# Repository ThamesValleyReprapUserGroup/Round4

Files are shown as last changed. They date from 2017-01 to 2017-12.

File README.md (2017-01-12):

This is the repro for Round 4.

Currently round 4 is a Mendel90 frame with a build volume of 200x200x200mm

But we have put our own twist's on it:

- All wires are run on top side of the base plate
- The endstop is a minimum endstop and not a maximum one
- The X carriage is Prusa I3 style
- The sheets can be used by both new builders and the ones that has a Round1-3 printer
- Builder has option to use either a 12V 30A type PSU or an ATX PSU
- The sheet also have holes for an optional enclosure found on thingiverse here: http://www.thingiverse.com/thing:755654 and here http://www.thingiverse.com/thing:744868

The reasons for this are:

- Wires run on the underside tends to get caught to easy and flop arround. And we can loose the alu tubes which again have very hard to print/use endcaps.
- Max mounted endstops have its advantages but you have to home up with them and hence you have to go all the way down again before you can print. 
- Going for the Prusa I3 carriage gives more options as a lot more have been build for it
- We aim to be able to provide a set of sheets which can suit both upgrades and new builds
- Giving the choice of PSU let's the builder choose free. ATX's needs to be modded to work right (need to dummy loads added)
- An enclosure is almost a MUST HAVE if you want to print in ABS and have good results. This is optional thou but the holes for it will be on the sheets

 The BOM is here, it might need some tweaks so it can change as we get closer: https://docs.google.com/spreadsheets/d/1C7syP7WIMzRRcczZF0KAYDTLpP77kqbQEB_rWFmMJsc/edit?usp=sharing

 CURRENT STATUS: Verifying printed parts
 ---------------------------------------

We want to test that all the printed parts come out right on a calibrated printer.

This is done by printing and then messure all nut traps etc against this info sheet: 

http://www.slideshare.net/tejasudas/dimensions-of-metric-hex-nuts

First batch of "test" parts has been printed with Form Futura Easyfil ABS at 235C and 110C on the bed.

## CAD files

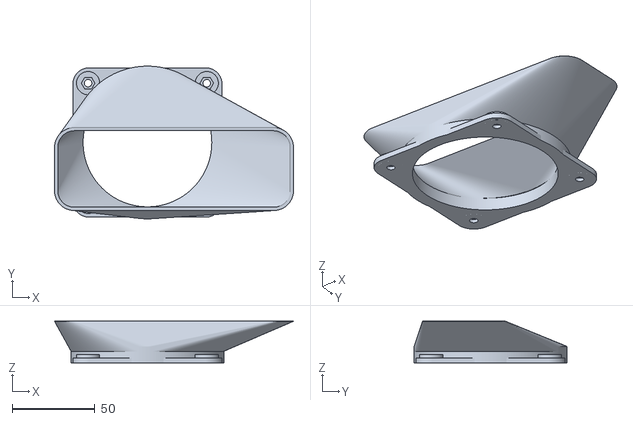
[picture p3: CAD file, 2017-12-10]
Mk42 Version/Printed Parts/Optinals/Bed fan duct/Mendel90_Fanduct_Heatbed.stl
144.0 x 92.0 x 25.1

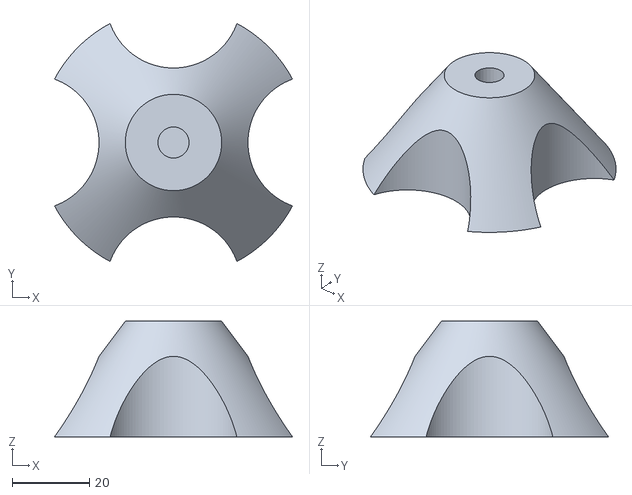
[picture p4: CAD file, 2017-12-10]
Mk42 Version/Printed Parts/Optinals/spool_holder.stl
61.8 x 61.8 x 30.0

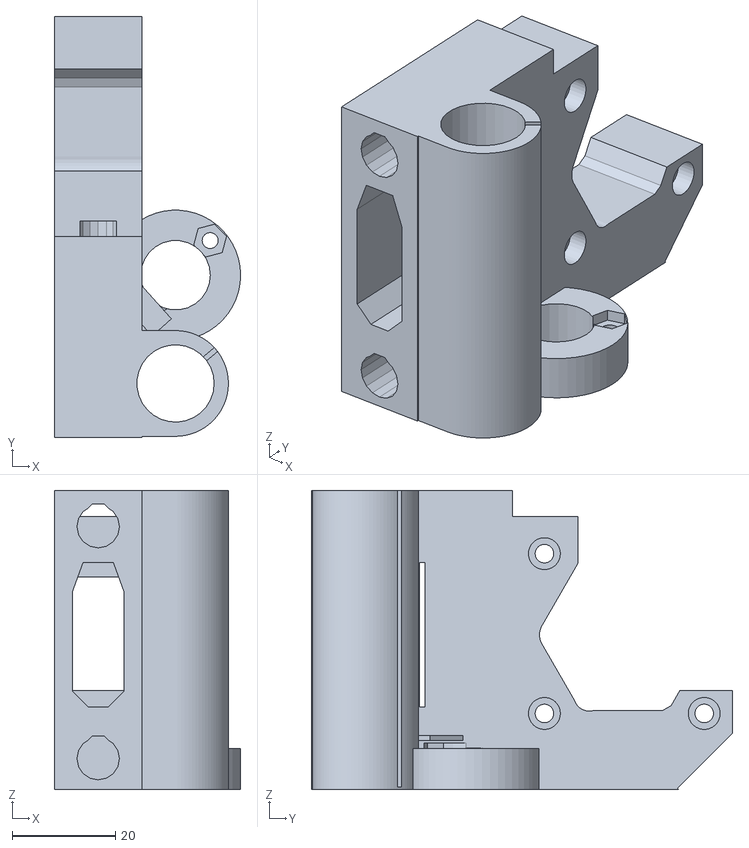
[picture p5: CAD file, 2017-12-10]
Mk42 Version/Printed Parts/X ends 2/x-end-motor.stl
36.1 x 81.7 x 58.0

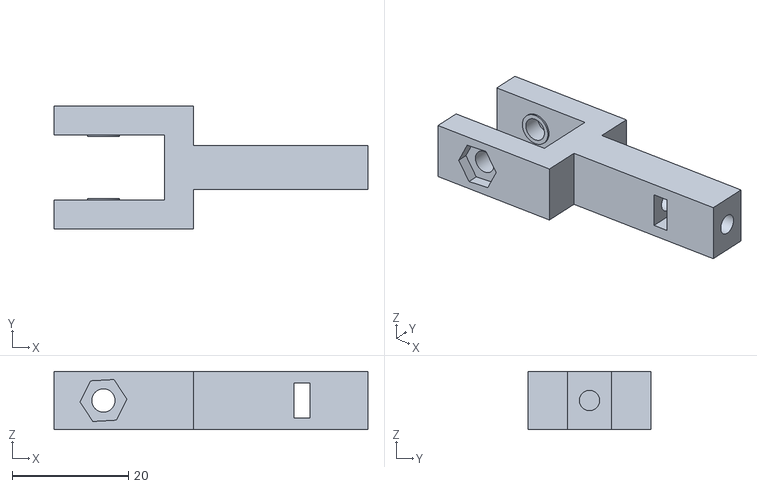
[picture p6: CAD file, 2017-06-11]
Mk42 Version/Printed Parts/Y Idler Fork.stl
54.0 x 21.2 x 10.0

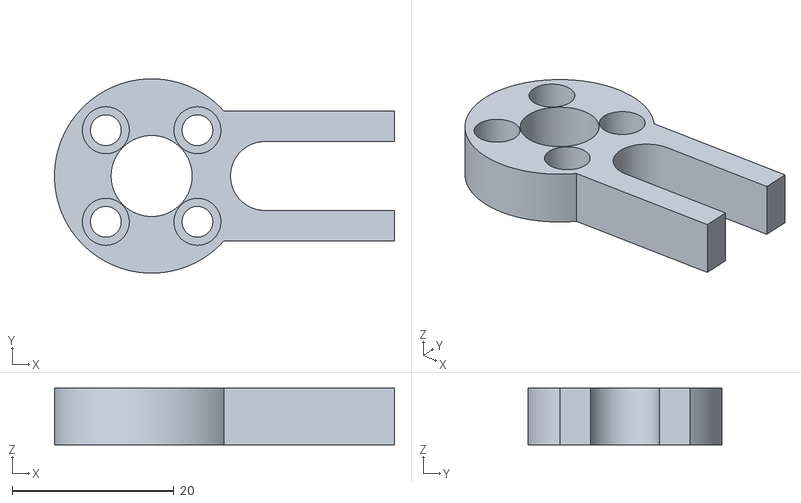
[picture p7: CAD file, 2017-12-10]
Mk42 Version/Printed Parts/Z isolators/dp-trapezoidal-zizolator.stl
42.0 x 24.0 x 7.00

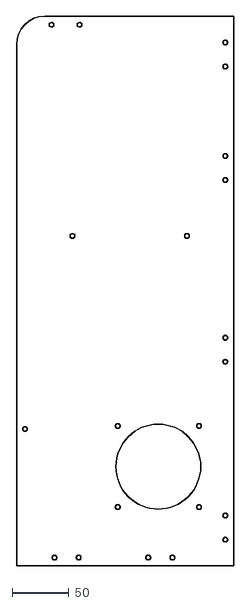
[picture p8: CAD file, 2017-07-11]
Mk42 Version/Sheets/frame_left_mk42_clean_fixed.dxf
191.1 x 484.0

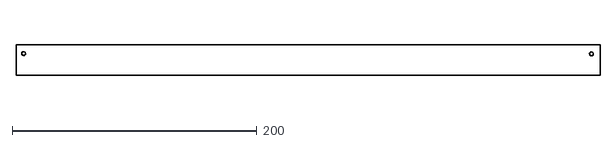
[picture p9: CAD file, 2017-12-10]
Mk42 Version/Sheets/Optional rear housing/coverplates_front_top_mk42_1.dxf
477.0 x 25.0

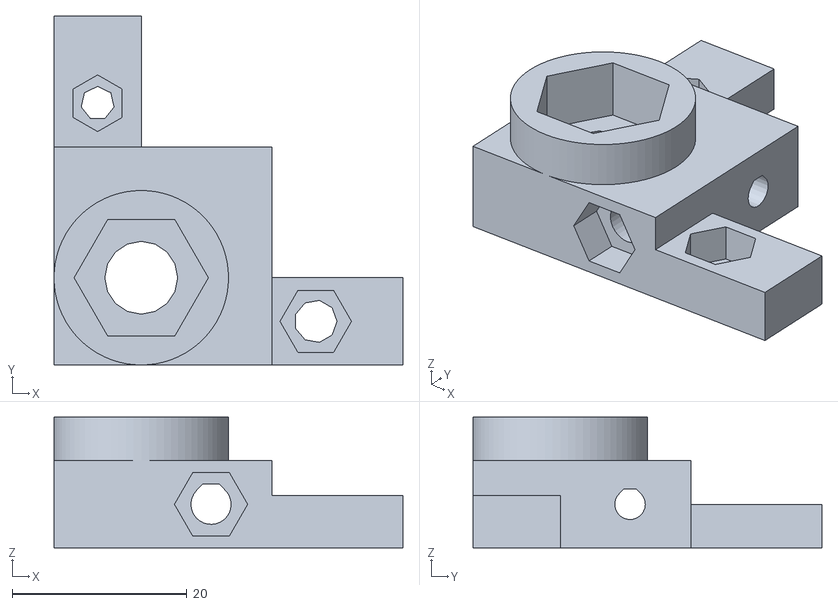
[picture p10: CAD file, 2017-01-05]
Calibration Prints/cal.stl
40.0 x 40.0 x 15.0

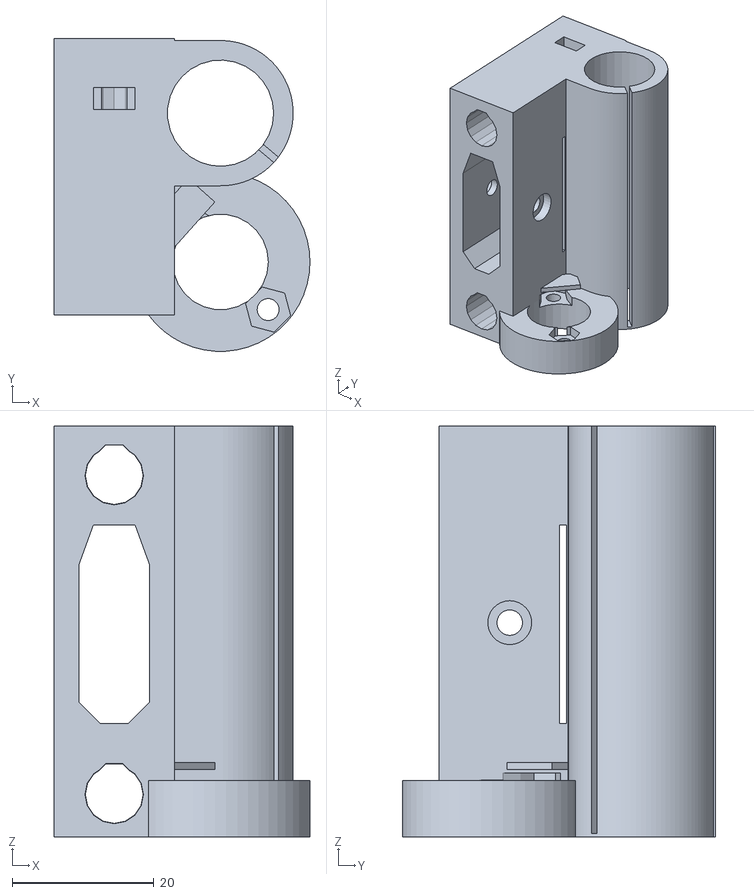
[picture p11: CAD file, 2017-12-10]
Mk42 Version/Printed Parts/X ends 2/x-end-idler.stl
36.1 x 44.1 x 58.0

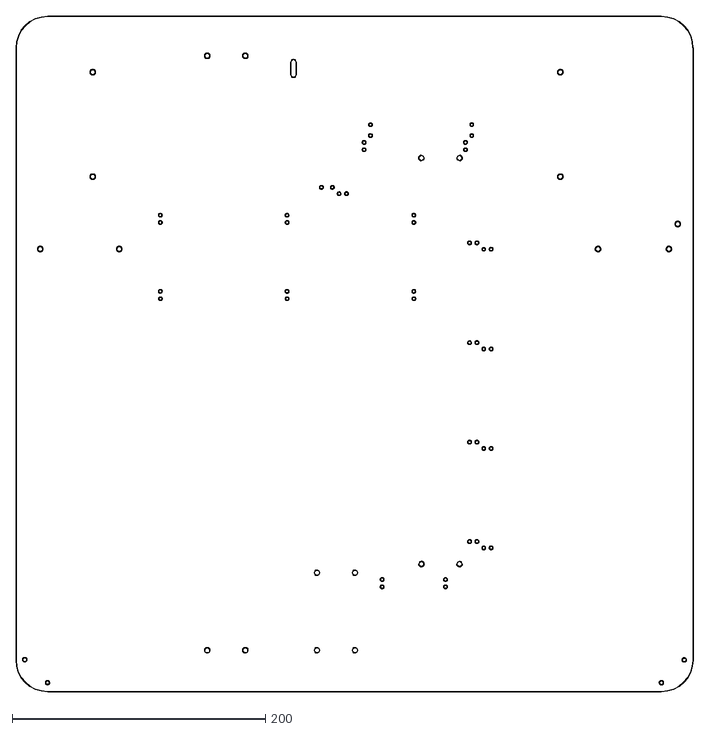
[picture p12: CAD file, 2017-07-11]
Mk42 Version/Sheets/frame_base_mk42_clean_fixed.dxf
534.2 x 532.7

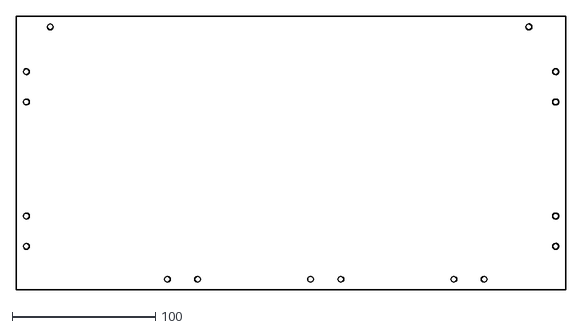
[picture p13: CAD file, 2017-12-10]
Mk42 Version/Sheets/Optional rear housing/coverplates_rear_2_mk42.dxf
383.8 x 190.7

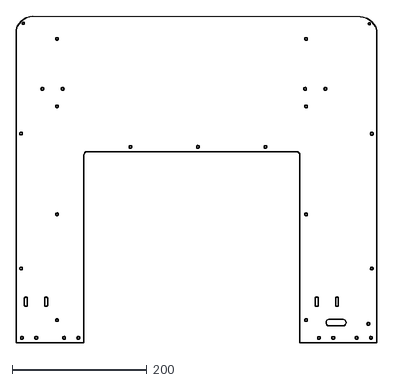
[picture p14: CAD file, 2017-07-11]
Mk42 Version/Sheets/frame_gantry_mk42_clean_fixed.dxf
534.4 x 483.9

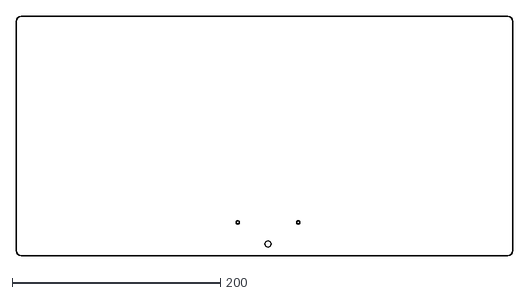
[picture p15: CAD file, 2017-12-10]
Mk42 Version/Sheets/Optional rear housing/coverplates_front_top_mk42_3.dxf
477.0 x 230.0

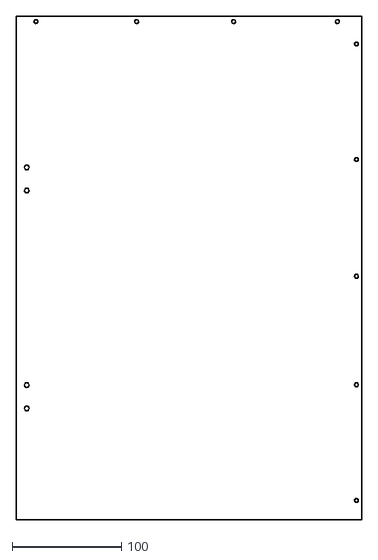
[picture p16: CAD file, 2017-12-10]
Mk42 Version/Sheets/Optional rear housing/coverplates_front_side_mk42.dxf
316.9 x 461.7

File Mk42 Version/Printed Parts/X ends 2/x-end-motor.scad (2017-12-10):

// PRUSA iteration3
// X end motor
// GNU GPL v3
// Josef Průša <iam@josefprusa.cz> and contributors
// http://www.reprap.org/wiki/Prusa_Mendel
// http://prusamendel.org

use <x-end.scad>
use <bearing.scad>
use <polyholes.scad>

module x_end_motor_base(){
 mirror([0,1,0])translate([0,18.2,0])x_end_base();
   
 translate(v=[-15,31,26.5]) cube(size = [17,44,53], center = true);
}

module x_end_motor_endstop_base(){
    translate([-23.5,-28.5,58]){
        difference(){
            // Base block
            cube([17,18.2,4]);
            // Nice edge
            translate([-1,10,10])rotate([-45,0,0])cube(20,20,20);
            } 
        }
}

module x_end_motor_endstop_holes(){
    translate([-23.5,-28.5,58]){
        translate([17/2,7.5,-3]){
            // Back screw hole for endstop
            translate([-4.75,0,0])cylinder(r=1,h=19,$fn=20);
            // Front screw hole for endstop
            translate([4.75,0,0])cylinder(r=1,h=19,$fn=20);
            }
        }
}

module x_end_motor_holes(){
 mirror([0,1,0])translate([0,18.2,0])x_end_holes();
 // Position to place
 translate(v=[-1,32,30.25]){
  // Belt hole
  translate(v=[-14,1,0]) cube(size = [10,46,22], center = true);
  // Motor mounting holes
  translate(v=[20,-15.5,-15.5]) rotate(a=[0,-90,0]) rotate(a=[0,0,90]) cylinder(h = 70, r=1.8, $fn=30);
  translate(v=[1,-15.5,-15.5]) rotate(a=[0,-90,0]) rotate(a=[0,0,90]) cylinder(h = 10, r=3.1, $fn=30);
  translate(v=[20,-15.5,15.5]) rotate(a=[0,-90,0]) rotate(a=[0,0,90]) cylinder(h = 70, r=1.8, $fn=30);
  translate(v=[1,-15.5,15.5]) rotate(a=[0,-90,0]) rotate(a=[0,0,90]) cylinder(h = 10, r=3.1, $fn=30);
   translate(v=[20,15.5,-15.5]) rotate(a=[0,-90,0]) rotate(a=[0,0,90]) cylinder(h = 70, r=1.8, $fn=30);
  translate(v=[1,15.5,-15.5]) rotate(a=[0,-90,0]) rotate(a=[0,0,90]) cylinder(h = 10, r=3.1, $fn=30);
  translate(v=[20,15.5,15.5]) rotate(a=[0,-90,0]) rotate(a=[0,0,90]) cylinder(h = 70, r=1.8, $fn=30);
  translate(v=[1,15.5,15.5]) rotate(a=[0,-90,0]) rotate(a=[0,0,90]) cylinder(h = 10, r=3.1, $fn=30);

  // Material saving cutout 
  translate(v=[-10,12,10]) cube(size = [60,42,42], center = true);

  // Material saving cutout
  translate(v=[-10,40,-30]) rotate(a=[45,0,0])  cube(size = [60,42,42], center = true);
  // Motor shaft cutout
  //#translate(v=[0,0,0]) rotate(a=[0,-90,0]) rotate(a=[0,0,90]) cylinder(h = 70, r=17, $fn=6);
 }
}

// Motor shaft cutout
module x_end_motor_shaft_cutout(){
    union(){
    difference(){
        translate(v=[0,32,30]) rotate(a=[0,-90,0]) rotate(a=[0,0,90]) cylinder(h = 70, r=17, $fn=6);
       
        translate(v=[-10,-17+32,30]) cube(size = [60,2,10], center = true);
        translate(v=[-10,-8+32,-15.5+30]) rotate(a=[60,0,0]) cube(size = [60,2,10], center = true); ///
        translate(v=[-10,8+32,-15.5+30]) rotate(a=[-60,0,0]) cube(size = [60,2,10], center = true);
        
        
    }
    translate(v=[-30,25.2,-11.8 +30]) rotate(a=[0,90,0]) cylinder(h = 30, r=3, $fn=30);
    translate(v=[-30,19.05,30]) rotate(a=[0,90,0]) cylinder(h = 30, r=3.5, $fn=100);
}
}




// Final part
module x_end_motor(){
 difference(){
     union(){
            x_end_motor_base();
            //x_end_motor_endstop_base();
         }
  x_end_motor_shaft_cutout();
  x_end_motor_holes();
  //x_end_motor_endstop_holes();    
      
      translate([-12,-42,65]) rotate([-35,0,0])  rotate([0,0,45]) cube(10,10,10);
      translate([-15,8.5,6]) rotate([90,0,0]) cylinder(h=5, r=5, $fn=30);   
      translate([-15,8.5,51]) rotate([90,0,0]) cylinder(h=5, r=5, $fn=30);   
      translate([-15,3.5,6]) rotate([90,0,0]) cylinder(h=3, r1=5, r2=4, $fn=30);   
      translate([-15,3.5,51]) rotate([90,0,0]) cylinder(h=3, r1=5, r2=4, $fn=30); 
      //#translate([-16,-40,0])cube([50,100,100]); 
        bearing_diameter = 14.5;
         thinwall = 3;
bearing_size = bearing_diameter + 2 * thinwall;
        
         
        translate(v=[0,-18.2,10]) poly_cylinder(h = 62, r=(bearing_diameter/2)+0.1);
         
 }
 
}

translate([0,-2.8,0])x_end_motor();

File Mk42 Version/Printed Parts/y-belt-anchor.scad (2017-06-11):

//
// Mendel90
//
// GNU GPL v2
// nop.head@gmail.com
// hydraraptor.blogspot.com
//
// Anchors the belt to the bottom of the y carriage
//
include <conf/config.scad>
include <positions.scad>

wall = 2;

clearance = 2;
thickness = M3_nut_trap_depth + bearing_clamp_tab_height;
rad = 3;

clamp_thickness = 2.8;

width = belt_width(Y_belt) + 3 + washer_diameter(M3_washer) + clearance;
inner_width = (M3_nut_radius + wall) * 2 ;
depth =  washer_diameter(M3_washer) + clearance;
length = depth + 2 * (2 * M3_nut_radius * cos(30) + wall);

tooth_height = belt_thickness(Y_belt) / 2;
tooth_pitch = belt_pitch(Y_belt);
tooth_width = tooth_pitch / 2;

function y_belt_anchor_width() = width;
function y_belt_anchor_depth() = depth;

module y_belt_anchor_holes() {
    for(side = [-1, 1])
        translate([0, side * (depth / 2 + M3_nut_radius * cos(30) + eta) + depth / 2, 0])
            children();

}

module y_belt_anchor(height, toothed) {
    h = height + belt_thickness(Y_belt) - belt_clearance;
    recess = length - depth;

    stl(str("y_belt_anchor", toothed ? "_toothed" : ""));
    union() {
        difference() {
            union() {
                translate([0, depth / 2, h / 2])                                                        // tall bit
                    rounded_rectangle([width, depth, h], r = rad);

                translate([0, depth / 2, thickness / 2])
                    rounded_rectangle([inner_width, length, thickness], r = rad);                       // wide bit

                for(side = [-1, 1])                                                                     // webs
                    for(end = [-1, 1])
                        translate([side * (M3_nut_radius + wall / 2 + eta), eta + (end + 1) * (depth / 2 - 2 * eta), thickness - eta])
                            rotate([90,0,90 * end])
                                right_triangle(width = (length - depth) / 2 - rad, height = h - thickness, h = wall);
            }


            translate([0, depth / 2, height + (h - height) / 2 + 2 * eta])                              // slot for belt
                cube([belt_width(Y_belt) + belt_clearance, depth + 1, h - height], center = true);

            for(side = [-1, 1]) {                                                                        // clamp screw nut traps
               # translate([side * (belt_width(Y_belt) / 2 + M3_clearance_radius), depth / 2, 0 ])
                    rotate([0,0,90/7 * (side + 1)])
                        nut_trap(M3_clearance_radius, M3_nut_radius+0.1, height - clamp_thickness);

                translate([0, side * (depth / 2 + M3_nut_radius * cos(30) + eta) + depth / 2, thickness])  // mounting screw nut traps
                    nut_trap(M3_clearance_radius, M3_nut_radius, M3_nut_trap_depth);

            }
            translate([0, depth / 2, height + (h - height) / 2 + 2 * eta])                                  // slot to join screw holes
                cube([belt_width(Y_belt) + M3_clearance_radius * 2, corrected_diameter(M3_clearance_radius * 2), h - height], center = true);
        }

        for(side = [-1, 1])                                                                                 // blind the nut traps
            translate([side * (belt_width(Y_belt) / 2 + M3_clearance_radius), depth / 2, height - clamp_thickness])
                cylinder(r =  M3_clearance_radius + 0.5, h = layer_height + eta);

        if(toothed)
            for(i = [-1:1])
                if(abs(i) * tooth_pitch + tooth_width / 2 < depth / 2)
                    translate([0, depth / 2 + i * tooth_pitch, height - eta + tooth_height / 2])
                        cube([belt_width(Y_belt), tooth_width, tooth_height], center = true);
    }
}

module y_belt_clip(toothed) {
    stl(str("y_belt_clip",  toothed ? "_toothed" : ""));

    union() {
        translate([0, 0, clamp_thickness / 2]) difference() {
            rounded_rectangle([width, depth, clamp_thickness], r = rad);

            for(side = [-1, 1])                                                                        // screw holes
                translate([side * (belt_width(Y_belt) / 2 + M3_clearance_radius), 0, 0 ])
                    poly_cylinder(r = M3_clearance_radius, h = clamp_thickness + 1, center = true);
        }
        if(toothed)
            for(i = [-1:1])
                if(abs(i) * tooth_pitch + tooth_width / 2 < depth / 2)
                    translate([0, i * tooth_pitch, clamp_thickness - eta + tooth_height / 2])
                        cube([belt_width(Y_belt), tooth_width, tooth_height], center = true);
    }

}

module y_belt_anchor_assembly(height, toothed) {
    //assembly("y_belt_anchor_assembly");

    color(y_belt_anchor_color) render() y_belt_anchor(height, toothed);

    translate([0, depth / 2, height + belt_thickness(Y_belt) + clamp_thickness]) {
        rotate([180, 0, 0])
            color(y_belt_clip_color) render() y_belt_clip(!toothed);
        //
        // Clamp screws
        //
        for(side = [-1, 1])
            translate([side * (belt_width(Y_belt) / 2 + M3_clearance_radius), 0, 0]) {
                screw_and_washer(M3_cap_screw, 16);
                translate([0, 0, -2 * clamp_thickness - belt_thickness(Y_belt)])
                    rotate([180, 0, 90/7 * (side + 1)])
                        nut(M3_nut, true);
            }
    }
    for(side = [-1, 1])
        translate([0, side * (depth / 2 + M3_nut_radius * cos(30) + eta) + depth / 2, 0]) {
            translate([0, 0, thickness - M3_nut_trap_depth])
                nut(M3_nut, true);
            translate([0, 0, - sheet_thickness(Y_carriage)])
                rotate([180, 0, 0])
                    screw_and_washer(M3_cap_screw, 16);
        }

    //end("y_belt_anchor_assembly");
}

module y_belt_anchor_stl()         y_belt_anchor(Y_belt_clamp_height, false);
module y_belt_anchor_toothed_stl() y_belt_anchor(Y_belt_clamp_height, true);
module y_belt_clip_stl()           y_belt_clip(false);
module y_belt_clip_toothed_stl()   y_belt_clip(true);

module y_belt_anchors_stl() {
    translate([0,  0, 0]) y_belt_anchor_toothed_stl();
    translate([0, 25, 0]) y_belt_anchor_stl();
//    translate([15, 5, 0]) rotate([0,0,90])y_belt_clip_toothed_stl();
//    translate([15,30, 0]) rotate([0,0,90]) y_belt_clip_stl();
}

//if(1)
  //  y_belt_anchor_assembly(Y_belt_clamp_height, true);
//else
    y_belt_anchors_stl();

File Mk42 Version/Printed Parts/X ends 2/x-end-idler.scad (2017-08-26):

// PRUSA iteration3
// X end idler
// GNU GPL v3
// Josef Průša <iam@josefprusa.cz> and contributors
// http://www.reprap.org/wiki/Prusa_Mendel
// http://prusamendel.org

use <x-end.scad>



module x_end_idler_holes(){
    x_end_holes();
    translate([0,3.5,0]){
    translate(v=[0,-22,30.25]) rotate(a=[0,-90,0]) cylinder(h = 80, r=1.8, $fn=30);
    translate(v=[1.5,-22,30.25]) rotate(a=[0,-90,0]) cylinder(h = 10, r=3.1, $fn=30);
    translate(v=[-21.5,-22,30.25]) rotate(a=[0,-90,0]) rotate(a=[0,0,30]) cylinder(h = 80, r=3.2, $fn=6);
        
 }
}


module waste_pocket(){
 // waste pocket
    translate([-15,-1,6]) rotate([90,0,0]) cylinder( h=5, r=5.5, $fn=30);     
    translate([-15,-1,51]) rotate([90,0,0]) cylinder( h=5, r=5.5, $fn=30);    
    translate([-15,-5.9,6]) rotate([90,0,0]) cylinder( h=3, r1=5.5, r2=4.3, $fn=30);     
    translate([-15,-5.9,51]) rotate([90,0,0]) cylinder( h=3, r=5.5, r2=4.3, $fn=30);      

    
    //M3 thread
    translate([-15,8.5,6]) rotate([90,0,0]) cylinder( h=12, r=1.4, $fn=30); 
    translate([-15,8.5,51]) rotate([90,0,0]) cylinder( h=12, r=1.4, $fn=30); 

    //M3 heads
    translate([-15,11.5,6]) rotate([90,0,0]) cylinder( h=4, r=2.9, $fn=30); 
    translate([-15,11.5,51]) rotate([90,0,0]) cylinder( h=4, r=2.9, $fn=30); 

    //M3 nut traps
    translate([-17.9,0.5,52-3-1.6]) cube([5.8,3.1,20]);
    translate([-17.9,0.5,-10+1.5+1.6]) cube([5.8,3.1,16]);
}


module x_end_idler_base(){
    union(){
        difference(){
            x_end_base();
            x_end_idler_holes();
        }
        translate([-15,8.5,6]) rotate([90,0,0]) cylinder( h=11, r=6, $fn=30);
        translate([-15,8.5,51]) rotate([90,0,0]) cylinder( h=11, r=6, $fn=30);
    }
}


module x_end_idler(){
    //mirror([0,1,0]) 
    difference(){
        x_end_idler_base();
        waste_pocket();
        
  // Bottom pushfit rod
translate(v=[-15,-31.2,6]) rotate(a=[-90,0,0]) pushfit_rod(7.8,41);
// Top pushfit rod
translate(v=[-15,-31.2,45+6]) rotate(a=[-90,0,0]) pushfit_rod(7.8,41);
    }
    
}
//difference(){
x_end_idler();
//translate([-15,-50,0])   cube([100,100,100]);
//}

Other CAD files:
Mk42 Version/Sheets/y_heatshield.dxf
Mk42 Version/Sheets/Optional rear housing/coverplates_rear_1_mk42.dxf
Mk42 Version/Sheets/y_heatshield_2.dxf
Mk42 Version/Printed Parts/X ends 2/x-end.scad
Calibration Prints/20140205_Marvin_KeyChain.STL
Mk2 version/Printed Parts/3edv6mount/Bowden_carriage.stl
Mk2 version/Printed Parts/3edv6mount/Bowden_carriage_clamp.stl
Mk2 version/Printed Parts/Optionals/Bed fan duct/Mendel90_Fanduct_Heatbed.scad
Mk2 version/Printed Parts/Optionals/Bed fan duct/Mendel90_Fanduct_Heatbed.stl
Mk2 version/Printed Parts/Optionals/Filament_holder.scad
Mk2 version/Printed Parts/Optionals/Filament_holder.stl
Mk2 version/Printed Parts/Optionals/Ramps Holder with 80mm fan option/arduino_carrier2p_base.stl
Mk2 version/Printed Parts/Optionals/Ramps Holder with 80mm fan option/carrier2p_frame.stl
Mk2 version/Printed Parts/Optionals/duet enclosure/Duet_enclosure.stl
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

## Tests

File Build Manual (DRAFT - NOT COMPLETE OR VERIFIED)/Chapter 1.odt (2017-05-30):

## 1. General Build Tips

- X is left / right. Y is backwards / forwards. Z is up / down.
- De-grease the rods. Acetone or methylated spirit works. Dont worry they will be oiled later.
- All screws have a plain washer where they meet the plastic/sheets, to spread the load and prevent the plastic being chewed up by the rotation of the screw head. Most fixings have a captive Nyloc nut to prevent them vibrating loose. It is very important that the nut is fully seated in the nut trap while the screw is inserted. They are quite a tight fit, so sometimes it is necessary to pull or push them in with a long screw.
- The X and Y bar clamps should not be over tightened, i.e. do not close the gap fully or the parts will break. The Y and Z bars only need a light clamping force because the only force trying to slide them is the bearing friction.
- Washers tend to have a smooth side and a side with a burr from being stamped out. Make sure the smooth side faces bearings and belts.

NOTE: During this manual 3mm fiberboard was used. It’s cheaper for prototyping.

NOTE: It’s optional, but might be a good idea to drill all holes to their spec’ed size. If a 4mm screw is used in the hole drill it to 4mm. Endstop switches normally 2.5 holes but you can drill them to 3mm if you talke care. This is the method used in this manual.

### Tools Required

- Allen keys: 1.5 & 2.5mm & 3mm
- Needle nose pliers.
- 8mm sharp drill bit
- 3mm
- 4mm
- 2mm
- Drill with variable speed
- Small hammer
- Marker or pen
- M3 tap
- Wire cutters.
- Wire strippers.
- Crimp tool for dupont connectors – You can solder but its not nearly as good as crimping

#### Recommended

- Multi-meter
- Digital callipers.
- Dial gauge and/or Set of feeler blades(to level the bed more - precise than paper method)
- Heat gun for heat shrink tubing… far better than lighter or soldering iron
- Ruler and square. Even thou it should be 90 degrees, it does not hurt to check.

#### Consumables

- oil, white lithium grease, alcohol (for cleaning bed), lint free wipes.

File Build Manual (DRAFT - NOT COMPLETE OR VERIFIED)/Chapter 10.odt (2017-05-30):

## 10. Y Carriage Assembly

### Vitamins

14 M3 cap screw x 16mm 1 Dibond sheet 216mm x 216mm x 3mm 3 LM8UU bearings | 14 Nyloc nut M3 14 Washer M3 x 7mm x 0.5mm 3 Zip-tie 100mm min length

### Printed parts


| | 3 y_bearing_mount.stl

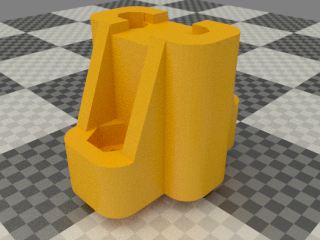
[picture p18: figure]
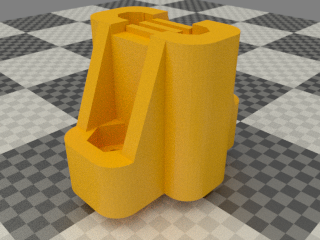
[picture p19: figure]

1 y_belt_anchor.stl | 1 y_belt_anchor_toothed.stl

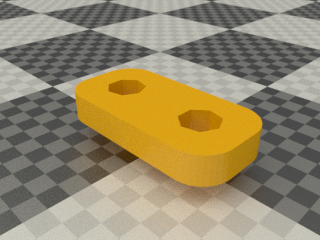
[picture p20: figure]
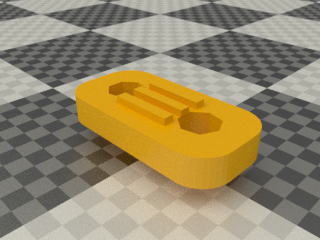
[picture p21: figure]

1 y_belt_clip.stl | 1 y_belt_clip_toothed.stl

### Assembly

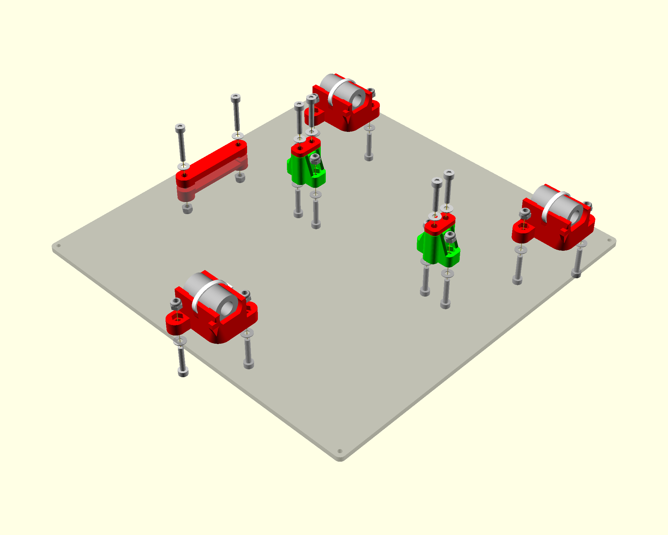
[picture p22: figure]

This view is from the bottom of the bed which is the matt side of the Dibond. The nuts go on the bottom and the screw heads and washers on top.

1. Insert M3 nyloc nuts into all of the nut traps, including those that go all the way up to the top of the belt anchors. A long M3 screw can be used to pull them up to the top.
2. Tie the bushingss into the holders with the zip ties, and screw the holders to the carriage using M3 x 16mm screws and washers. Note that one side of the bearing holders has a tab to trigger the limit switch and that must face forwards (that is, away from the ribbon clamp).
  TIP: use the square to help make the rod and holders parallel to the edge
3. Align the two bearings on the left (right on the picture) by inserting a rod and lining up the tabs with the edge of the board before tightening the screws. Leave the third bearing loose.
4. Fit the belt clamps loosely to retain the nuts using M3 x 16mm screws and washers, then fit the anchors to the carriage using M3 x 16mm screw and washers. Note that the anchor with the teeth goes at the back (nearest to the ribbon clamp) and the belt clamp with the teeth at the front.

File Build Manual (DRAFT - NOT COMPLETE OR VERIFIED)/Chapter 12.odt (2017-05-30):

## Print bed assembly

### Vitamins

1 PCB bed mk42 4 M3 cap screw x 10mm 6 Hex male / female pillar M3 x 20mm | 2 Heatshrink sleeving ID 1.6mm x 15mm 2 Heatshrink sleeving ID 2.4mm x 15mm 2 Heatshrink sleeving ID 6.4mm x 30mm 4 Washer M3 x 7mm x 0.5mm 1 Black wire 32/0.2 length 635mm 1 Red wire 32/0.2 length 620mm

### Sub-assemblies

1 y_carriage_assembly

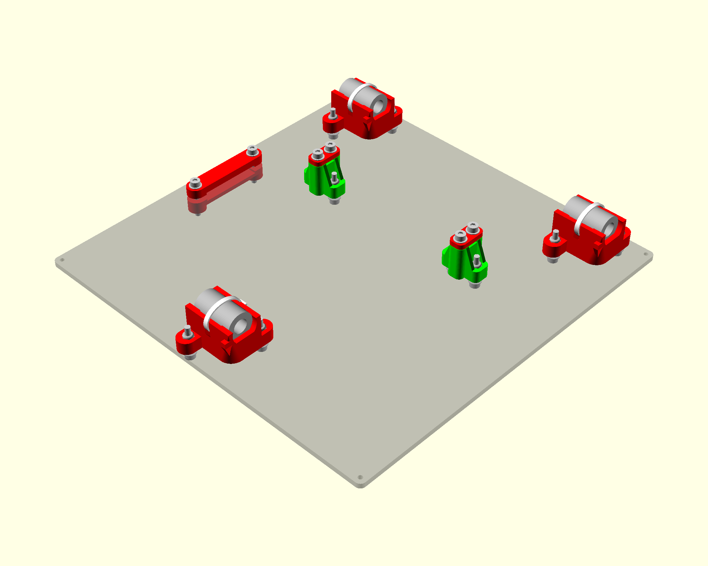
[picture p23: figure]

### Bed Wiring

1. Solder the red wire to the positive terminal and the black to negative.
2. Place a strip of kapton tape where the thermistor wires will go.
3. Use kapton tape to tape down the thermistor. Place the thermistor at the center hole. Don’t force it in but just let it rest there.
4. Use red and black wires trimmed from the X motor for the thermistor wiring extension.
5. Insert the hex screws at each corner and the 2 near the center
6. mount the heat bed with 6 countersink screws
7. attach the wires to the zip ties to the holes going from the corner towards the center.
8. Fold the wires over the edge near the center and attach to carraige with the holes going from the edge at the center towards the center

### Assembly

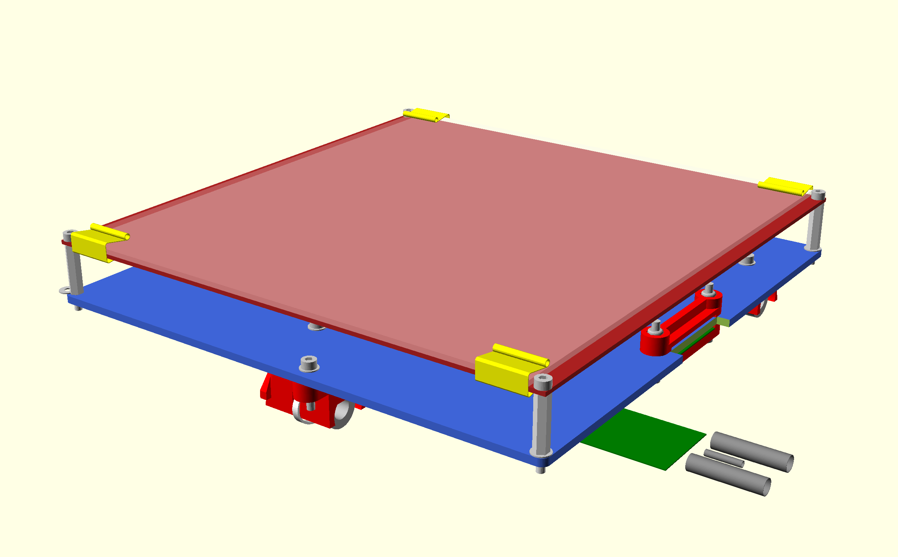
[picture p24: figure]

1. Tap the corner holes and the 2 center holes to 3mm. Screw the pillars into the Y carriage, but don't over tighten as it is quite soft. Note that the rear two pillars have a washer under them. The front two are initially spaced the same distance by using a washer as a temporary shim. They can then be adjusted up or down slightly to level the bed relative to the nozzle.
2. The bed is installed with the cable at the back. It initially leads off forwards and then loops back on itself under the top ribbon clamp. It then doubles back under the Y carriage through the lower cable clip.
3. Screw the bed to the top of the pillars with the M3 x 10 cap screws (no washers). Just start the screws as you will need to take the bed off again to tighten the last bearing holder. This is best done when belt etc. are in place

TO BE DONE: DP notes says to use button head screws as they reduce height and interference with HE and then no PP strip used?

4. Pull the ribbon cable tight enough so that the loop under the bed does not touch the bed and clamp it together with the polypropylene strip (which goes closest to the clamp).

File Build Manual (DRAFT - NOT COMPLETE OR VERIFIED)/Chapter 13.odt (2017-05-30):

## Y Axis Assembly

### Vitamins

1 Belt GT2 x 6mm x 662mm 4 M3 cap screw x 16mm 8 M4 cap screw x 16mm 4 Nyloc nut M3 8 Nyloc nut M4 2 No2 pan wood screw x 13mm | 1 Smooth rod 8mm x 270mm 1 Smooth rod 8mm x 417mm 1 Microswitch 2 Washer M2.5 x 5.9mm x 0.5mm 4 Washer M3 x 7mm x 0.5mm 8 Washer M4 x 9mm x 0.8mm

### Printed parts

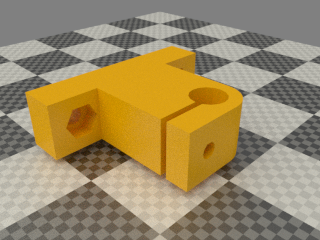
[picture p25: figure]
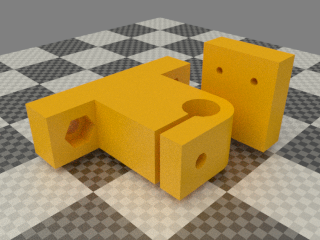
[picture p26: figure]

3 y_bar_clamp.stl | 1 y_bar_clamp_switch.stl

### Sub-assemblies

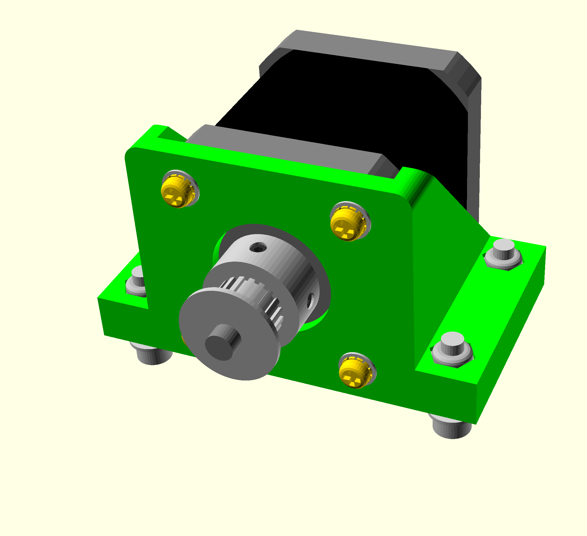
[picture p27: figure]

1 print_bed_assembly | 1 y_idler_assembly | 1 y_motor_assembly

### Assembly


1. Drill the 2 small holes in the switch bar clamp to 2.5mm
2. tap the holes to 3mm
3. Insert the captive nyloc M3 nuts and M3 x 16mm cap screws in each of the Y bar clamps.
4. Loosely fit the two left hand Y bar clamps to the base. Orientate them so the rod is towards the outside of the machine.
5. Twist together two green wires about 750mm long (trimmed from the X motor) and solder them to the outer two pins of the microswitch. Reem out the holes in the microswitch and attach it to the barclamp with M3 screws with M3 screws BUT NO wshers as it would prevent the smooth rod from going in the bar clamp. Remember the button towards the top and facing the back of the machine.
6. Fit the right hand Y bar clamps to the base but leave the screws loose.
7. Thread the limit switch wires through the zip ties and through mouse hole in the right stay.
8. Also thread the Y motor wires through the zip ties in the base and then screw the Y motor bracket in place. Run the wires in the cable ties and holes parallel to the limit switch wires.
9. Clamp the Y belt in the front belt anchor with the teeth facing away from the carriage. The end of the belt should project enough to have five complete teeth showing.
10. Put a half twist in the belt and then thread it through the Y idler assembly with the smooth side against the bearings and then clamp it in the rear clamp with the teeth facing the carriage. Again leave five complete teeth projecting from the anchor.
11. Slide the Y bars through the bar clamps and the carriage bearings. Tighten the clamps to grip the bars lightly but do not over-tighten them. Slide the carriage up and down to align the right hand bearing and bar clamps. Tighten the bearing first and then move it to each end and tighten the clamps.
12. Put the belt over the motor pulley and fasten the idler assembly to the base with enough tension on the belt to play a low note when plucked. Ensure the belt runs in the middle of the idler without touching the washers each side by adjusting the angle of the idler.
13. Attach the wires from the bed so that it forms a loop. The middle of the loops points towards the Y motor.
14. The wires turn right and go through the cable ties and under the mouse holes in the right hand stay. The heater wires go through the rear tie and the larger hole.

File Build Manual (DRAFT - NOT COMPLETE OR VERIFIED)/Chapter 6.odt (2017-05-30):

## 6 Motor Assemblies

### Vitamins

2 M3 cap screw x 16mm 4 M3 cap screw x 12mm 4 M4 cap screw x 16mm 2 NEMA17 x 47mm stepper motor 6 Nyloc nut M3 | 4 Nyloc nut M4 8 M3 cap screw x 10mm 14 Washer M3 x 7mm x 0.5mm 4 Washer M4 x 9mm x 0.8mm 8 Star washer M3 x 0.5mm

### Printed parts


1 z_motor_bracket_lhs.stl | 1 z_motor_bracket_rhs.stl


2 z-axis_lead_screw_clamp.stl

### Assembly

1. Fit all the nyloc nuts into their nut traps.
2. Fit the M3 x 16mm cap screws to the bar clamps with plain washers.
3. Attach the motor using four M3 x 10mm cap screws, star washers and plain washers. Wires from the left hand motor routes on top of the base to the left and meets up with the wires from the Y motor and goes through the gantry and under the right stay. The wires from the right hand motor goes through the wide slot just behind it.
4. Degrease the motor shafts before fitting the Z coupling, but be very carefull you dont get degreaser down the shaft in the steppers. Holding them upside down should help
5. Fit the coupling loosely for now. Insert a M3 screw and washer but do not tighten fully
6. Twist the motor wires in pairs. Red / blue are one pair and green / black the other pair. The quickest way to twist them is by using an electric drill. Tie a knot in the far end and put it in the chuck. The reason they are twisted is to minimise the radio frequency emissions.
7. Attach the motor assemblies to the gantry using M4 x 16mm cap screws and washers. Note that the motors rest on the base and the bar clamps face inwards.


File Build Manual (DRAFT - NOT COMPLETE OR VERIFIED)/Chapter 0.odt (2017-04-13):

# Mendel90 Instructions

The build is broken down into sub assemblies that can be worked on sequentially by one person, or in parallel if there is more than one person building. For this reason each assembly begins on a new page so the instructions can be separated.

15-11-12 First release of this manual.

25-11-12 Made Z cable 100mm longer. Added advice about temperatures.

03-12-12 Fixed missing Z parts. Added Skienforge and bed sections.

30-11-12 Z bar clamps and Y bearing mounts no longer have separate switch versions.

21-12-12 T2.5 belt and pulleys, new extruder PCB and Jhead mount.

02-01-13 Minor corrections and suggestions from users.

03-03-13 Removed feed tube connector.

14-03-13 Updates from user feed back and latest part renders.

21-03-13 Added section on using other software.

20-05-13 Added warning about absolute extrusion.

12-09-13 New X ends, Z couplers and fan bracket.

18-09-13 New file locations, SF profile, etc.

01-10-13 Updated remaining assembly views for black screws and red silicone on hot end.

18-11-13 Added instruction to fit nut and grub screw to extruder gear.

12-01-14 Fixed erroneous reference to hex screws in X motor assembly.

17-01-14 Added requirement for Philips screwdriver for removing X and E motor screws.

Fixed erroneous z_min instead of z_max.

17-01-14 Clarified changing E_STEPS_PER_MM expression.

27-07-14 Small corrections and clarifications.

07-09-14 Fixed a few typos.

14-10-14 Fixed more typos.

12-03-15 Added bed cooling fan wiring details.

08-06-15 Changed belts and pulleys to GT2

02-08-16 Changed by tvrrug.co.uk to have all wires run on top of the base. This makes the wire runs as short as possible and makes the chances of wires getting caught less.

02-08-16 Changed by tvrrug.co.uk to use the Prusa I3 X carriage system but with the X motor still on the right.

02-08-16 Changed by tvrrug.co.uk to use the Mk42 Bed.

02-08-16 Changed by tvrrug.co.uk to not use cable clamps. They are replaced with silicone/rubber wires held in place with zipties at each end

Table of Contents

1.General Build Tips 6

Tools Required 8

Recommended 8

Consumables 8

2.Frame Assembly 9

Vitamins 9

Printed parts 9

Assembly 10

3.Bed Fan Assembly 13

Vitamins 13

Printed part 13

Assembly 13

4.X Idler Assembly 15

Vitamins 15

Printed 15

Assembly 16

5.X Motor Assembly 17

Vitamins 17

Printed parts 17

Assembly 18

6.Z Motor Assemblies 23

Vitamins 23

Printed parts 23

Assembly 24

7.Z Axis Assembly 26

Vitamins 26

Printed parts 26

Sub-assemblies 26

Assembly 27

8.Y idler assembly 29

Vitamins 29

Printed parts 29

Assembly 29

9.Y motor assembly 30

Vitamins 30

Printed parts 30

Assembly 31

10.Y Carriage Assembly 32

Vitamins 32

Printed parts 32

Assembly 33

11.Y Heatshield Assembly 34

Vitamins 34

Assembly 34

12.Print bed assembly 35

Vitamins 35

Sub-assemblies 35

Bed Wiring 36

Assembly 38

13.Y Axis Assembly 39

Vitamins 39

Printed parts 39

Sub-assemblies 39

Assembly 40

14.X Carriage Fan Assembly 42

Vitamins 42

Printed parts 42

Assembly 42

15.X Carriage Assembly 43

Vitamins 43

Printed parts 43

Assembly 44

16.Hot end assembly 45

Vitamins 45

Assembly 45

17.Extruder connection PCB assembly 47

Vitamins 47

Assembly 47

18.Extruder Motor Assembly 48

Vitamins 48

Printed parts 48

Sub-assemblies 48

Assembly 49

19.Extruder Assembly 51

Vitamins 51

Printed parts 51

Sub-assemblies 51

Assembly 52

20.X Axis Assembly 55

Vitamins 55

Sub-assemblies 55

Assembly 56

21.Spool holder assembly 58

Vitamins 58

Printed parts 58

Assembly 59

22.PSU assembly 60

Vitamins 60

Printed parts 60

Wiring 61

Summary 62

Assembly 63

23.Electronics Assembly 64

Vitamins 64

Printed Parts 64

Assembly 64

24.Software 68

Marlin Firmware 68

Arduino IDE 68

Pronterface 68

25.Testing 70

Jumpers 70

Power up 70

Limit switches 70

Motors 70

Heaters 71

Fan 71

26.Calibration 72

Bed Levelling 72

Extruder Calibration 73

Z Home Point 73

First Print 74

Slicing with Skeinforge 75

Extrusion Limits 76

27.Operating Instructions 77

Heated Bed 77

Changing filament 77

Removal 77

Insertion 78

Different types of filament 78

Cleaning the hobbed bolt 79

Using Other Software Tools 80

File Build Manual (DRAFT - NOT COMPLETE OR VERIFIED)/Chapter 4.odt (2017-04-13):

## 4 X Idler Assembly

### Vitamins

2 Ball bearing 624 4mm x 13mm x 5mm 2 LM8UU bearings 1 M3 cap screw x 35mm 1 M4 cap screw x 25mm 1 M3 cap screw x 18mm 1 Nyloc nut M3 | 1 Nyloc nut M4 2 Washer M3 x 7mm x 0.5mm 2 Washer M4 x 9mm x 0.8mm 1 Nut M3 1 M5 Brass nut

### Printed


1 i3xends_v2_Idler.stl | 1 i3xends_v2_Idler_fork.stl | 1 z_screw_isolator_left.stl

REPLACE 624 normal bearings with flanged type. Fork can rotate and belt will rub on the plastic. Also there is only so much room

LONGER M3 screw needed for for the idler fork

### Assembly

1. Slide the 2 Idler parts together, they are a VERY tight fit. Don’t worry if they don’t slide completely together. When inserting the X rods they will home the last bit.
2. Insert a M3 Nut in the idler fork. Slide it in the idler bits and insert a M3 35mm cap screw with a washers from the end of the idler, make sure the screw engange the nut corretcly.
3. Insert the M4 screw and washer through the fork while adding in the following order: 2 624 bearings. Once the screw is through add the final M4 washer and then M4 nyloc.

TIP: wipe the bearings off with paper tissue before mounting them. There might be grease on them. DONT use alcohol etc. just paper tissue and elbow grease-

TIP: if the bearings are loose on the screw add equal amount of M4 washers on the outside of each bearing until the assembly fits snug

4. Insert 2 LM8UU bearings, one from the top and one from the bottom.
5. Insert a M5 brass nut in the isolator. Put a M3 screw and washer through the isolator and a M3 Nyloc on the other side.
6. You should end up with this (note – the bearings was not at hand when making the manual):


7. Put these to a side for now

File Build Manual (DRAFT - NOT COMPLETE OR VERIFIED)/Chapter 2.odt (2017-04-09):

## 2. Frame Assembly

### Vitamins.

48 M4 cap screw x 16mm 2 Dibond sheet ?mm x ?mm x 3mm 1 Dibond sheet ?mm x ?mm x 3mm 1 Dibond sheet ?mm x ?mm x 3mm | 48 Nyloc nut M4 48 Washer M4 x 9mm x 0.8mm 29 Zip-tie 100mm min length

### Printed parts


16 fixing_block.stl

### Assembly


Note that this view is from the back of the machine.

1. Remove the protective film from the Dibond panels. They all have a matt side and a shiny side. The shiny side is up on the base, forward on the gantry and outside on the stays.
2. Insert M4 nyloc nuts into each of the three nut traps in the fixing blocks (a small pair of snipe nose pliers is useful for pressing them home).

TIP: You can also use the nose pliers to hold the nyloc while tighten the screws. Once they starts to seat in the fixing block you should be able to put down the pliers,

3. Loosely attach twelve fixing blocks to the left and right stays with two M4 x 16mm screws and washers each, noting that they go on the matt side that faces inwards.
4. Stand each sheet on its edges on a flat surface and slide the block down to be flush with the edge before tightening the screws. Tighten just enough to nip the sheets together but don't over-tighten.
5. Fit the remaining four fixing blocks along the bottom of the back of the gantry (large n shaped sheet) in the same way.
6. Fix the stays to the back of the gantry using one screw in each fixing block. Note the shiny sides face outwards and the one with the fan hole is on the left hand side looking from the front. Tighten the screws.
7. Loosely screw the gantry to the base using M4 x 16mm screws and washers from below into the nut traps in the fixing blocks.
8. Loosely insert ties into the pairs of small holes in the right stay and base. The joins should be under the base and on the right stay towards the left stay.
9. Use a square to check that all sheets stand on a 90 angle to each other. It can take some fiddle work to get them at right angles but the better the frame is the better and more easy the rest of the build will be.


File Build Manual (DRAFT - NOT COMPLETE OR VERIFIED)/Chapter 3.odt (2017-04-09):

## 3. Bed Fan Assembly

  The bed fan is optional. It lowers the cool down period when the parts are finished.

### Vitamins

4 M4 cap screw x 34mm 1 Fan 80mm x 26mm | 4 Nyloc nut M4 4 Washer M4 x 9mm x 0.8mm

### Printed part


1 fan_guard.stl

### Assembly


Make sure the fan is blowing inwards. This is usually indicated by an arrow on the frame and is often the side with the label.

The four screws pass through a plain washer, the fan guard, the left stay, the fan and finally a nyloc nut.

Twist the wires and route them on top of the base to electronics bay

It should look like this when done


Note that there has been added extra washers. Thou not required it will help spread the load on the fan when its added.

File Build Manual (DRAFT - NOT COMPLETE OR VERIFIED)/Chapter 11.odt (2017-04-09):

## Y Heatshield Assembly

The heatshield insulates the bottom surface of the heated bed to allow it to get hot enough for ABS. It isn't needed for printing PLA . If you want to print ABS it can be added later as it just slides under the bed. It is simply made from enough layers of corrugated cardboard to fill the air gap. The bottom layer has holes cut in it to clear the screws heads on the y-carriage and a slot to clear the ribbon cable. The higher layers just need the slot. The top layer will need an additional slot to clear the thermistor.

### Vitamins

1 Corrugated cardboard 192mm x 216mm x 5mm.

### Assembly


(http://reprap.org/wiki/File:Mendel90-Heatshield.png)

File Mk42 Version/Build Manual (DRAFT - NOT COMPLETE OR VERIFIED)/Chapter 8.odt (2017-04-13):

## Y idler assembly

### Vitamins

TO NARROW: use flanged bearings and add as many M4 washers as there is room for. Remember to try and use equal amounts of washer on each side of the bearings so they are centered

2 Ball bearing 624 4mm x 13mm x 5mm 1 M4 cap screw x 16mm 1 M4 cap screw x 30mm | 2 Nyloc nut M4 5 Washer M4 x 9mm x 0.8mm 2 Washer M5 x 20mm x 1.4mm

### Printed parts

1 y_idler_bracket.stl


### Assembly


Assemble as shown, easiest done on its side with the long axle screw pointing upwards and slowly inserted as the washers and bearings are added. To get the last washer in you have to have the bolt just far enough up to retain the M4 washer as the penny washer slides over it.

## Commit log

2017-01-05 Adding a calibration print and text file explaning it
    [cal.stl]
2017-01-05 Added Nopheads recommended print parameters
2017-01-05 changed * to x in build volume as they do not print when using markdown formatting
2017-01-12 First batch of tested parts
    Also includes the DRAFT of the first 6 chapters of the build manual.
    Manual needs to be tested throughly and build pictures added.
    [fan_guard.stl, fixing_block.stl, i3xends_v2 - Idler fork.stl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]
2017-01-14 next small batch of the printed parts
    They will come in odd order to optimize filament spool useage
    [ribbon_clamp_26_33.stl, ribbon_clamp_26_33N.stl, y_belt_anchor.stl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]
2017-01-18 updates to manual and added more parts
    [20140205_Marvin_KeyChain.STL, ABSSlurryPuck.STL, Arm.STL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]
2017-01-18 adeed source list for printed parts
2017-02-13 a few printed parts and build manual
    [atx_long_bracket.stl, atx_short_bracket.stl, z_bar_clamp.stl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]
2017-02-26 added draft version of wade extruder
    [Idler_with_guide.stl, big_gear.stl, cold_end_fan.stl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]
2017-03-15 a few files for extruder
    [boxes.scad, uploads-77-d1-a4-82-bf-z-probe-endstop-holder.scad, uploads-c0-4c-79-aa-0a-Filament_holder.scad]
2017-03-19 updated sheets
    2 more versions. 1 set provides full 200mm travel in all directions. and
    one more set that supports the mk42 bed.
    [BODY-EXTRUDEUR-WADE-1.75mm-with-support.stl, BODY-EXTRUDEUR-WADE-with-support.stl, Filament_holder.scad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]
2017-03-27 moved mk42 version in subfolder
    [frame_base_mk42_clean.dxf, frame_gantry_mk42_clean.dxf, frame_left_mk42_clean.dxf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]
2017-04-09 build manual moved to sub folder
    Chapter 2 should also be done now
    [BODY-EXTRUDEUR-WADE-1.75mm-with-support.stl, BODY-EXTRUDEUR-WADE-with-support.stl, Duet_enclosure.stl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]
2017-04-13 a few bits adjusted as mk42 is assembled on fiberboard
    [frame_base_mk42_clean_fixed.dxf, frame_gantry_mk42_clean_fixed.dxf, frame_left_mk42_clean_fixed.dxf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]
2017-05-30 updated build manual
    [Bowden_carriage.stl, Bowden_carriage_clamp.stl, Duet_enclosure.stl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]
2017-06-11 mk2 version build manual added
    [i3xends_v2 - idler.stl]
2017-06-11 mk2 version printed parts and sheets added
    [BODY-EXTRUDEUR-WADE-1.75mm-with-support.stl, BODY-EXTRUDEUR-WADE-with-support.stl, Bowden_carriage.stl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]
2017-06-11 mk42 sheets rename
    [coverplates_front_side_mk42.dxf, coverplates_rear_1_mk42.dxf, coverplates_rear_2_mk42.dxf]
2017-06-11 mk42 printed parts cleanup
    [Y Idler Fork.stl, bearing.scad, dp-trapezoidal-zizolator.scad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]
2017-06-11 remove full 200mm - now called mk2
    [coverplates_front_door_R15.dxf]
2017-07-11 moved build manual up one folder
    we only need one build manual
    [MessUhrHalter.stl, coverplates_front_top_mk42_2.dxf, coverplates_front_top_mk42_3.dxf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]
2017-08-26 updated sheets for mk2 version
    [bearing.scad, cover_plate_top_1_mk2.dxf, frame_base_mk2.dxf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]
